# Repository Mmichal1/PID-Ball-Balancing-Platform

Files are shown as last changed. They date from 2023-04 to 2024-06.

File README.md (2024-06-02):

# PID Ball Balancing Platform

Dual-axis ball balancing platform. The ball's location on the platform, relative to the center, is detected using a vision system, while the platform's tilt is controlled by a PID controller in each axis. This controller determines the positions of the servo mechanisms to maintain the ball at the center of the platform. Image processing and the PID controllers are implemented on a Raspberry Pi 4 mini-computer with a Raspberry Pi camera, and the servo mechanisms are controlled indirectly through serial port communication with an Arduino Uno.

## Ball detection and localization

Localization of the ball is carried out by analyzing the image received from the camera using the OpenCV library. The center of the platform is determined by ArUco markers placed at the corners of the platform. The intersection of diagonals drawn from the extreme points determines the center. Then, the position of the ball in the image is determined and the vector of the ball's displacement relative to the center of the platform is established.

### Detection

The position of the ball on the image is determined in 3 steps:

- Apply mask that brings out the pixel values within the specified HSV range.

<p align="center">
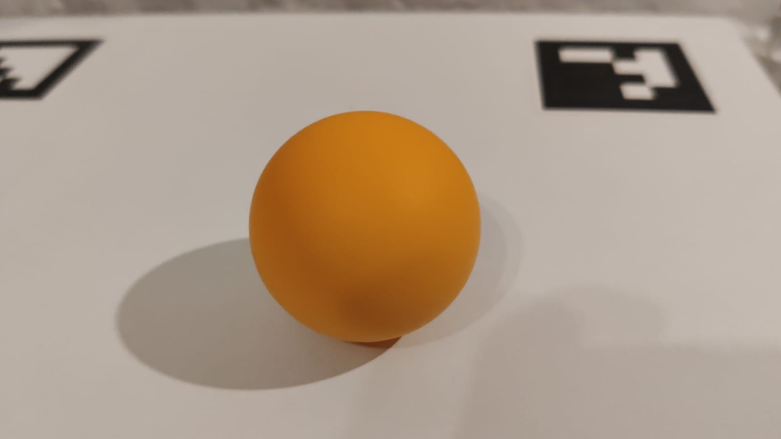
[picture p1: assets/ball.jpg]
  
</p>

<p align="center">
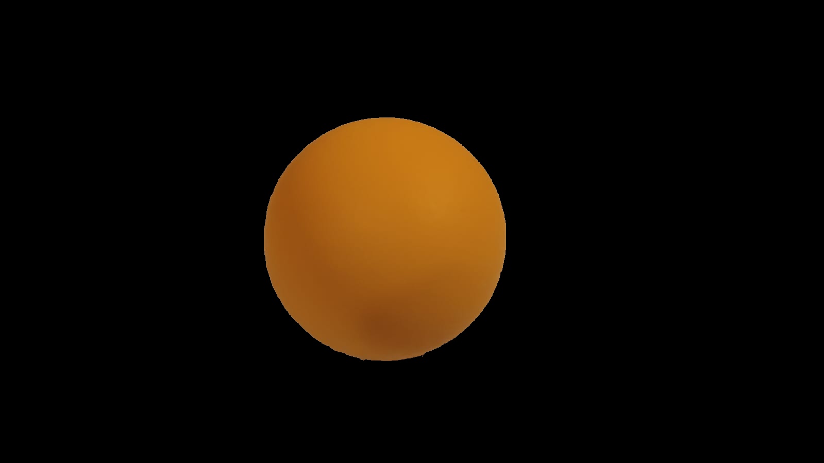
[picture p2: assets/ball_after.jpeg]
  
</p>

- Find contours on the image.
- Return the center biggest contour by area which is assumed to be the ball.

This works assuming that no objects with a color similar to the color of the ball are visible in the frame.

### Localization

The first step in the localization of the ball is determining the center of the platform. This is done using ArUco markers. After the center of the platform is determined, the distance of the ball in both axes in regard to the center of the platform is calculated.

<p align="center">
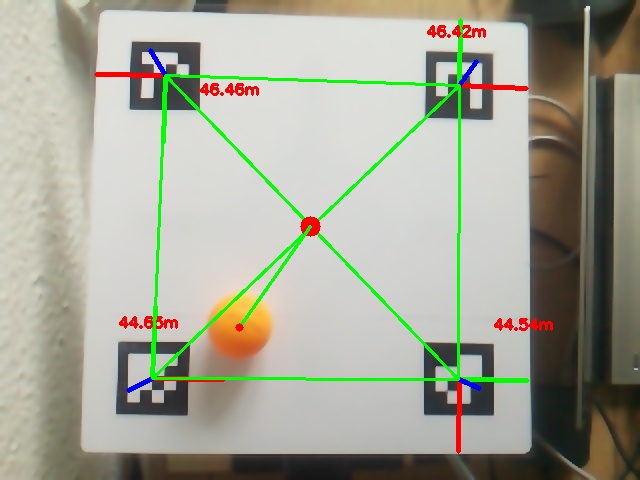
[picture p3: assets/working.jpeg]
  
</p>

The center of the platform is remembered in case any of the markers is covered by the ball.

<p align="center">
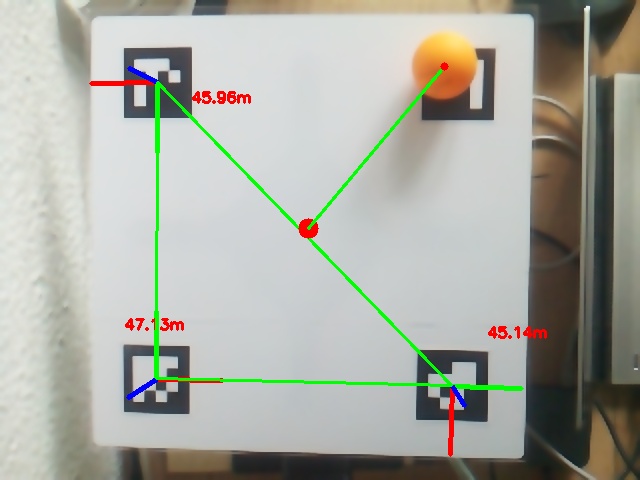
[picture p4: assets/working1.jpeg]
  
</p>

## Balancing

The ball is balanced in each axis independently by two PIDs based on the distance from the center using servomechanisms that tilt the platform accordingly. The input to the regulator is the distance from the center of the platform and the output is the position of the servomechanism. Tuning the regulator was done manually. Final regulation constants are as follows:

- Kp = 0.38
- Ki = 0.022
- Kd = 0.1

## Platform Construction

Most elements were modeled using Fusion 360 and 3D printed. All models and drawings can be found in `/technical_drawings` directory.

All elements were glued to a wooden base. The camera stand was constructed using aluminium profiles. The platform is a plexi glass panel.

<p align="center">
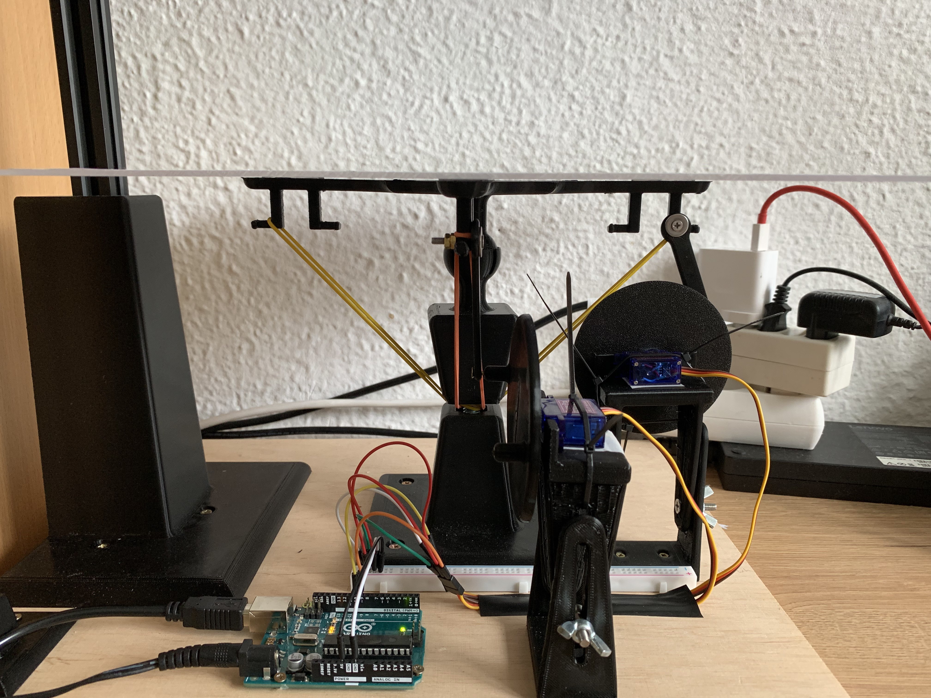
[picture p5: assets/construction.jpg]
  
</p>

<p align="center">
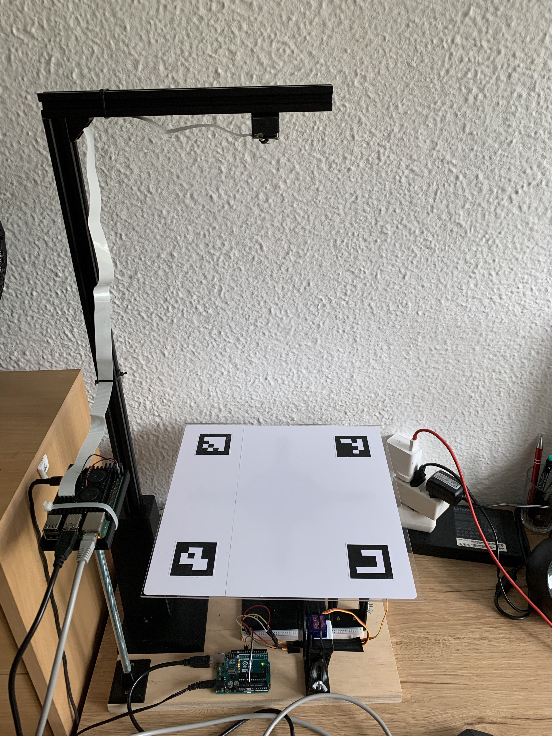
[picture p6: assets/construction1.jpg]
  
</p>

## Operation

A video showcasing the balancing platform operation has been uploaded to [YouTube](https://youtu.be/hny_5dCIR1Q).

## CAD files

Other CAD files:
technical_drawings/3d_models/Montaż_kamery.dwg
technical_drawings/3d_models/lacznik_kulkowy.dwg
technical_drawings/3d_models/Zewnetrzny_stojak.dwg
technical_drawings/3d_models/gora_platformy.dwg
technical_drawings/3d_models/Koło.dwg
technical_drawings/3d_models/wewnetrzny_stojak.dwg
technical_drawings/3d_models/Montaż_ramienia.dwg
technical_drawings/3d_models/Podstawa_platformy.dwg
technical_drawings/3d_models/Koło.ipt
technical_drawings/3d_models/Montaż_kamery.ipt
technical_drawings/3d_models/Montaż_ramienia.ipt
technical_drawings/3d_models/Podstawa_platformy.ipt
technical_drawings/3d_models/Zewnetrzny_stojak.ipt
technical_drawings/3d_models/gora_platformy.ipt
technical_drawings/3d_models/lacznik_kulkowy.ipt
technical_drawings/3d_models/podstawa raspberry.ipt
technical_drawings/3d_models/stolik raspberry.ipt
technical_drawings/3d_models/wewnetrzny_stojak.ipt

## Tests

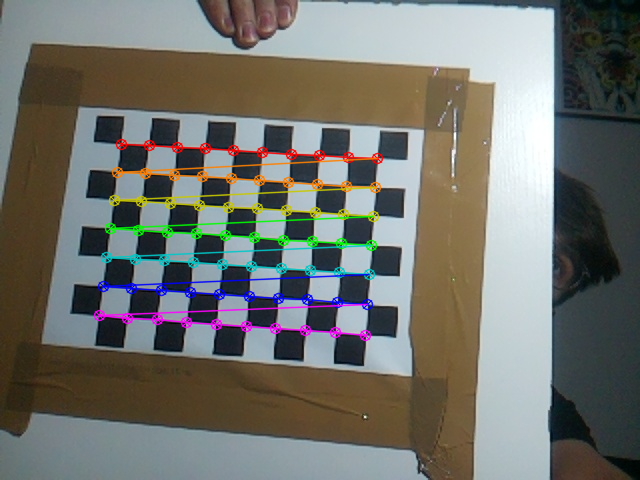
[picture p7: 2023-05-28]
camera_calibration/output_images/chessboard_corners_20230528_203139.png

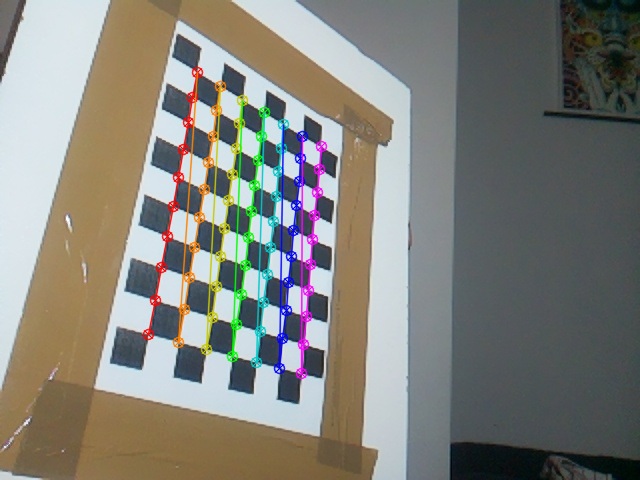
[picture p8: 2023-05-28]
camera_calibration/output_images/chessboard_corners_20230528_203134.png

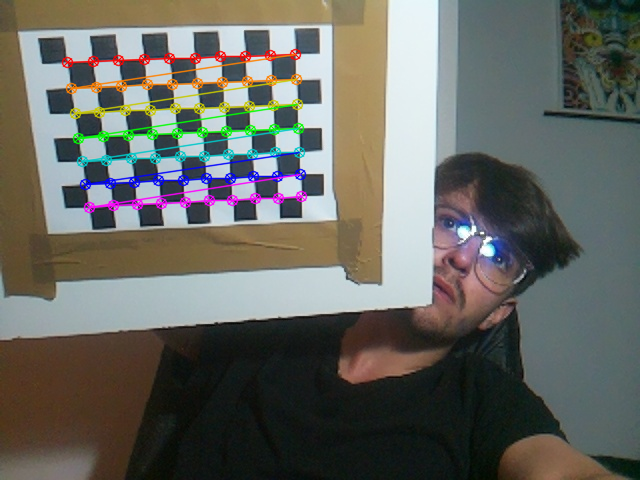
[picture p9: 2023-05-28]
camera_calibration/output_images/chessboard_corners_20230528_203137.png

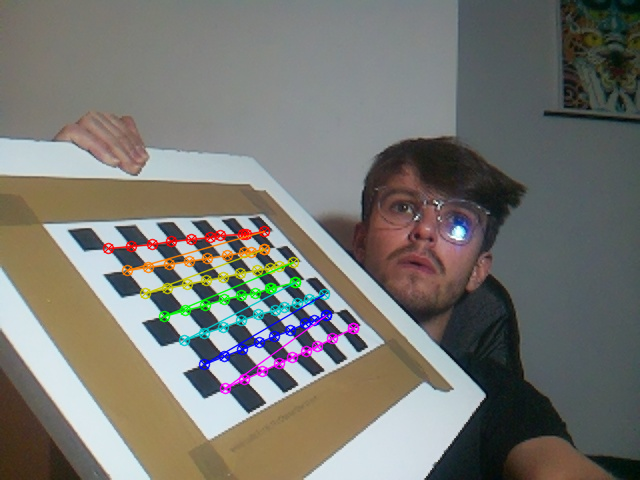
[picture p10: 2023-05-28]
camera_calibration/output_images/chessboard_corners_20230528_203148.png

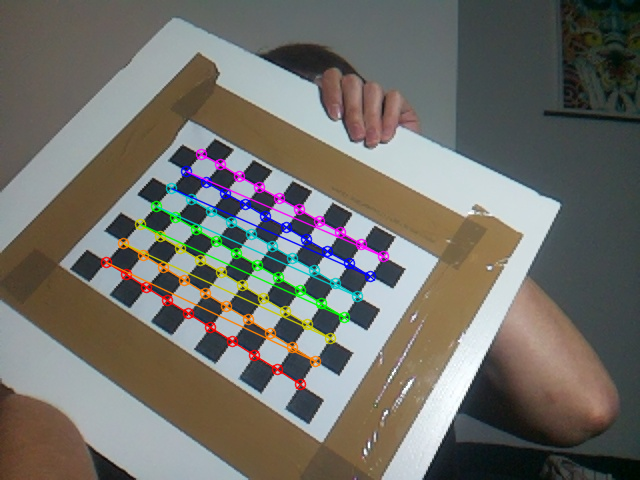
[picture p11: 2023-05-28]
camera_calibration/output_images/chessboard_corners_20230528_203145.png

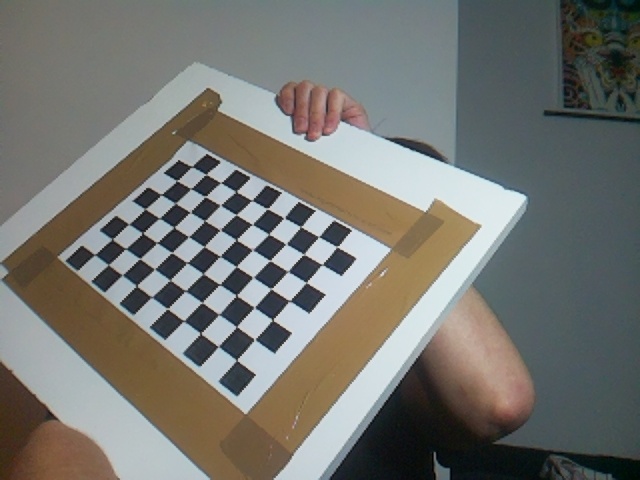
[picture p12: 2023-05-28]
camera_calibration/source_images/camera_13.jpeg

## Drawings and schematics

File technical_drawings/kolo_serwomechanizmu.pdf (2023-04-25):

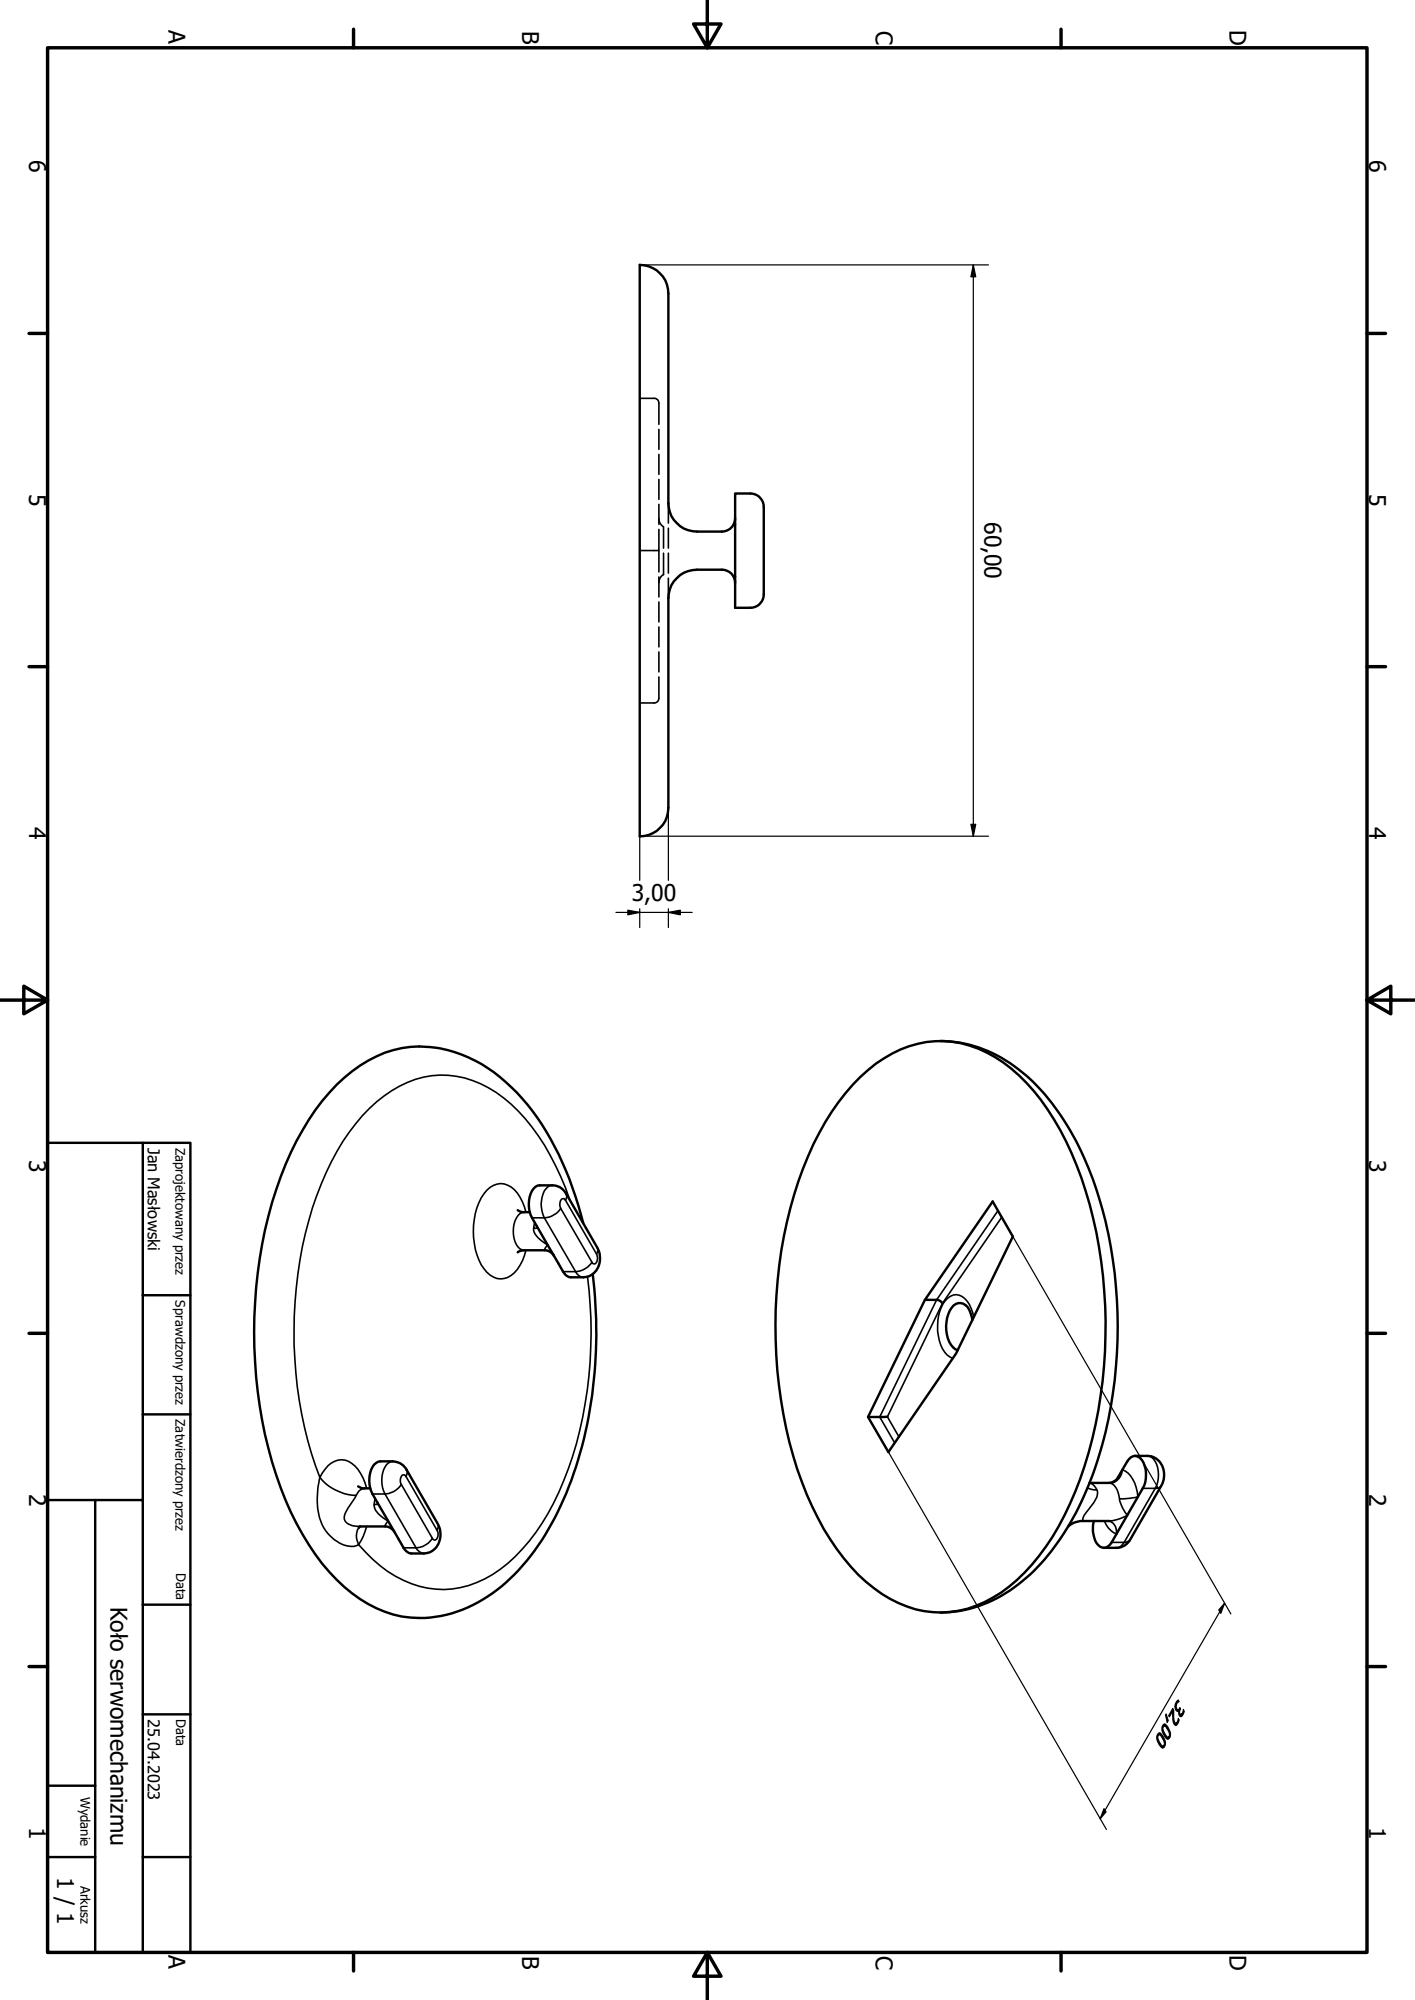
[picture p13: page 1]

11 22 33 44 55 66 A A B B C C D D Koło serwomechanizmu Jan Masłowski 25.04.2023 Zaprojektowany przez Sprawdzony przez Zatwierdzony przez Data 1 / 1 Wydanie Arkusz Data 60,00

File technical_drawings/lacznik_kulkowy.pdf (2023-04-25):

40,00 | 29,94 | 15,00

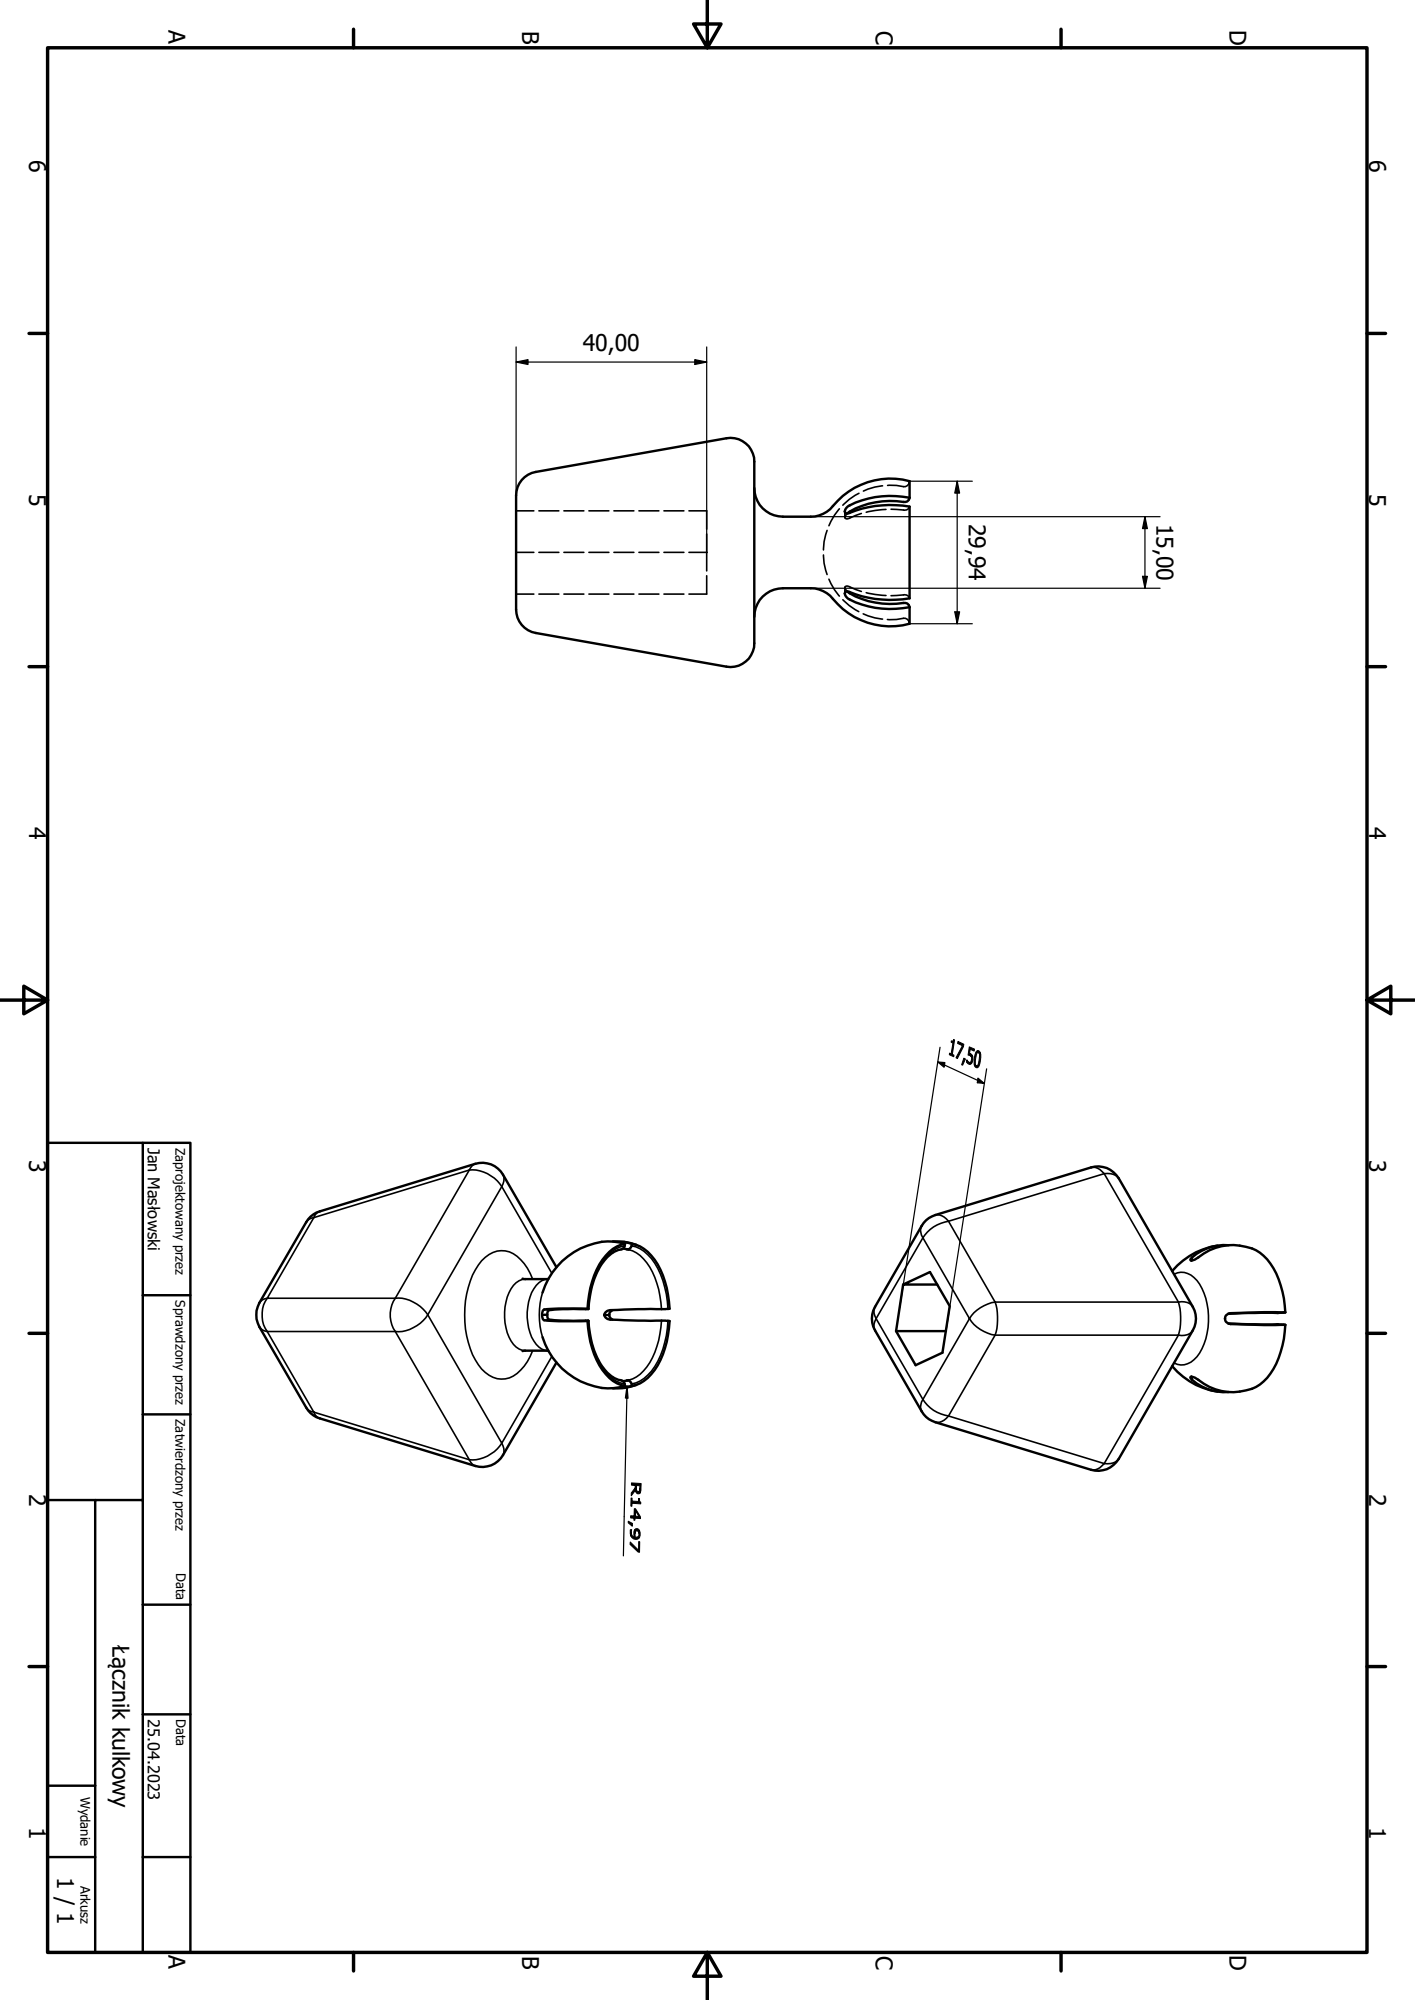
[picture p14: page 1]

D D C C B B A A 66 55 44 33 22 11 Data Arkusz Wydanie 1 / 1 Data Zatwierdzony przez Sprawdzony przez Zaprojektowany przez 25.04.2023 Jan Masłowski Łącznik kulkowy

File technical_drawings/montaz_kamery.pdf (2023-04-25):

6,00

12,17

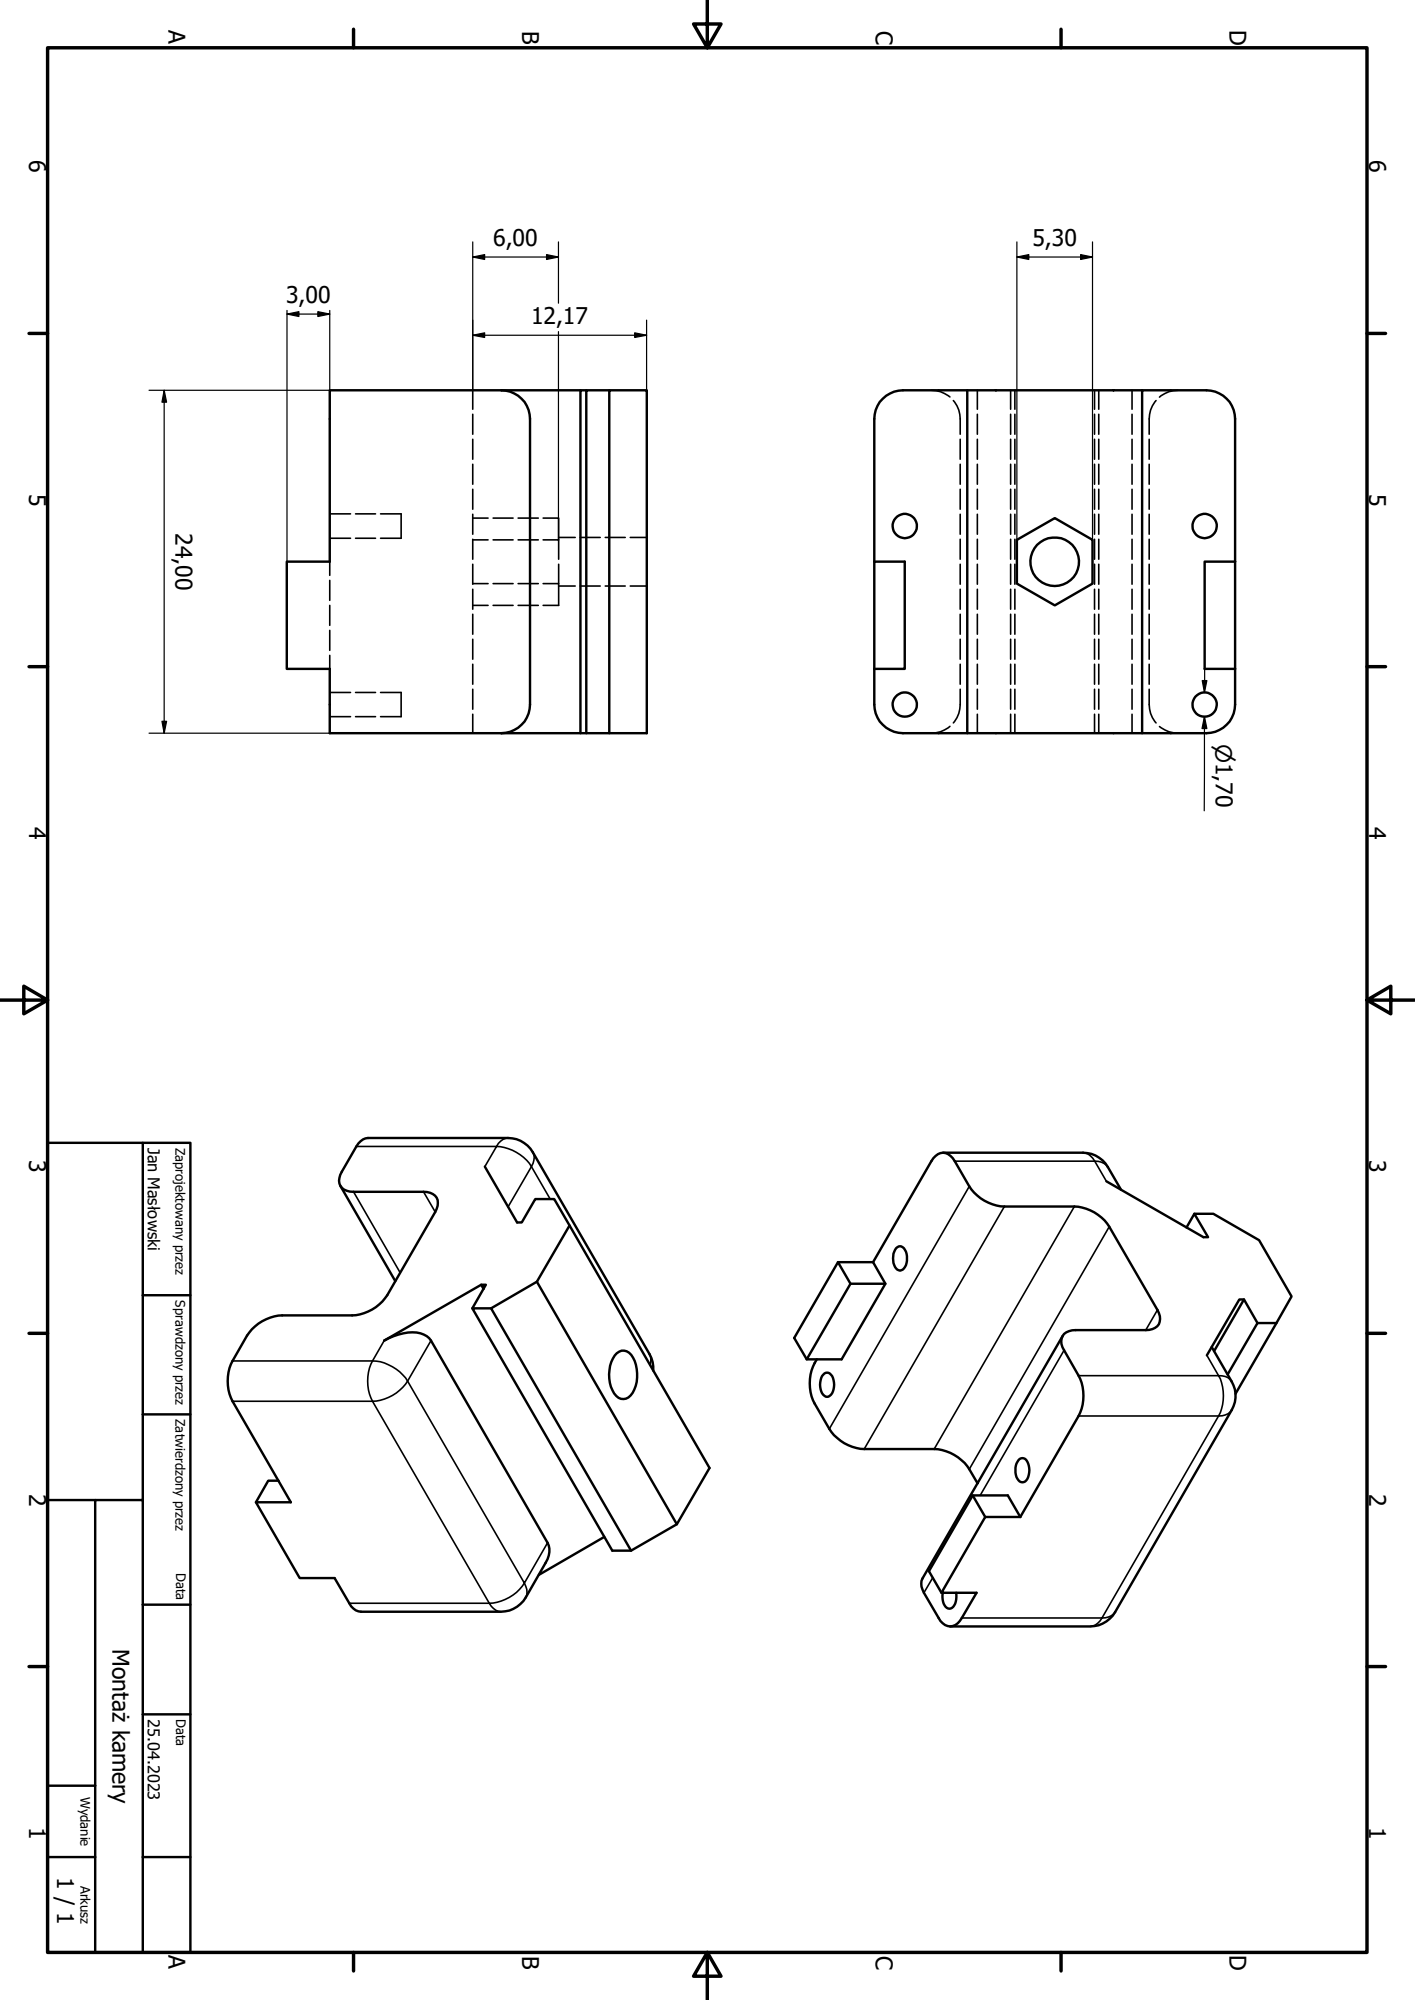
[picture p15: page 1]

11 22 33 44 55 66 A A B B C C D D Montaż kamery Jan Masłowski 25.04.2023 Zaprojektowany przez Sprawdzony przez Zatwierdzony przez Data 1 / 1 Wydanie Arkusz Data 24,00

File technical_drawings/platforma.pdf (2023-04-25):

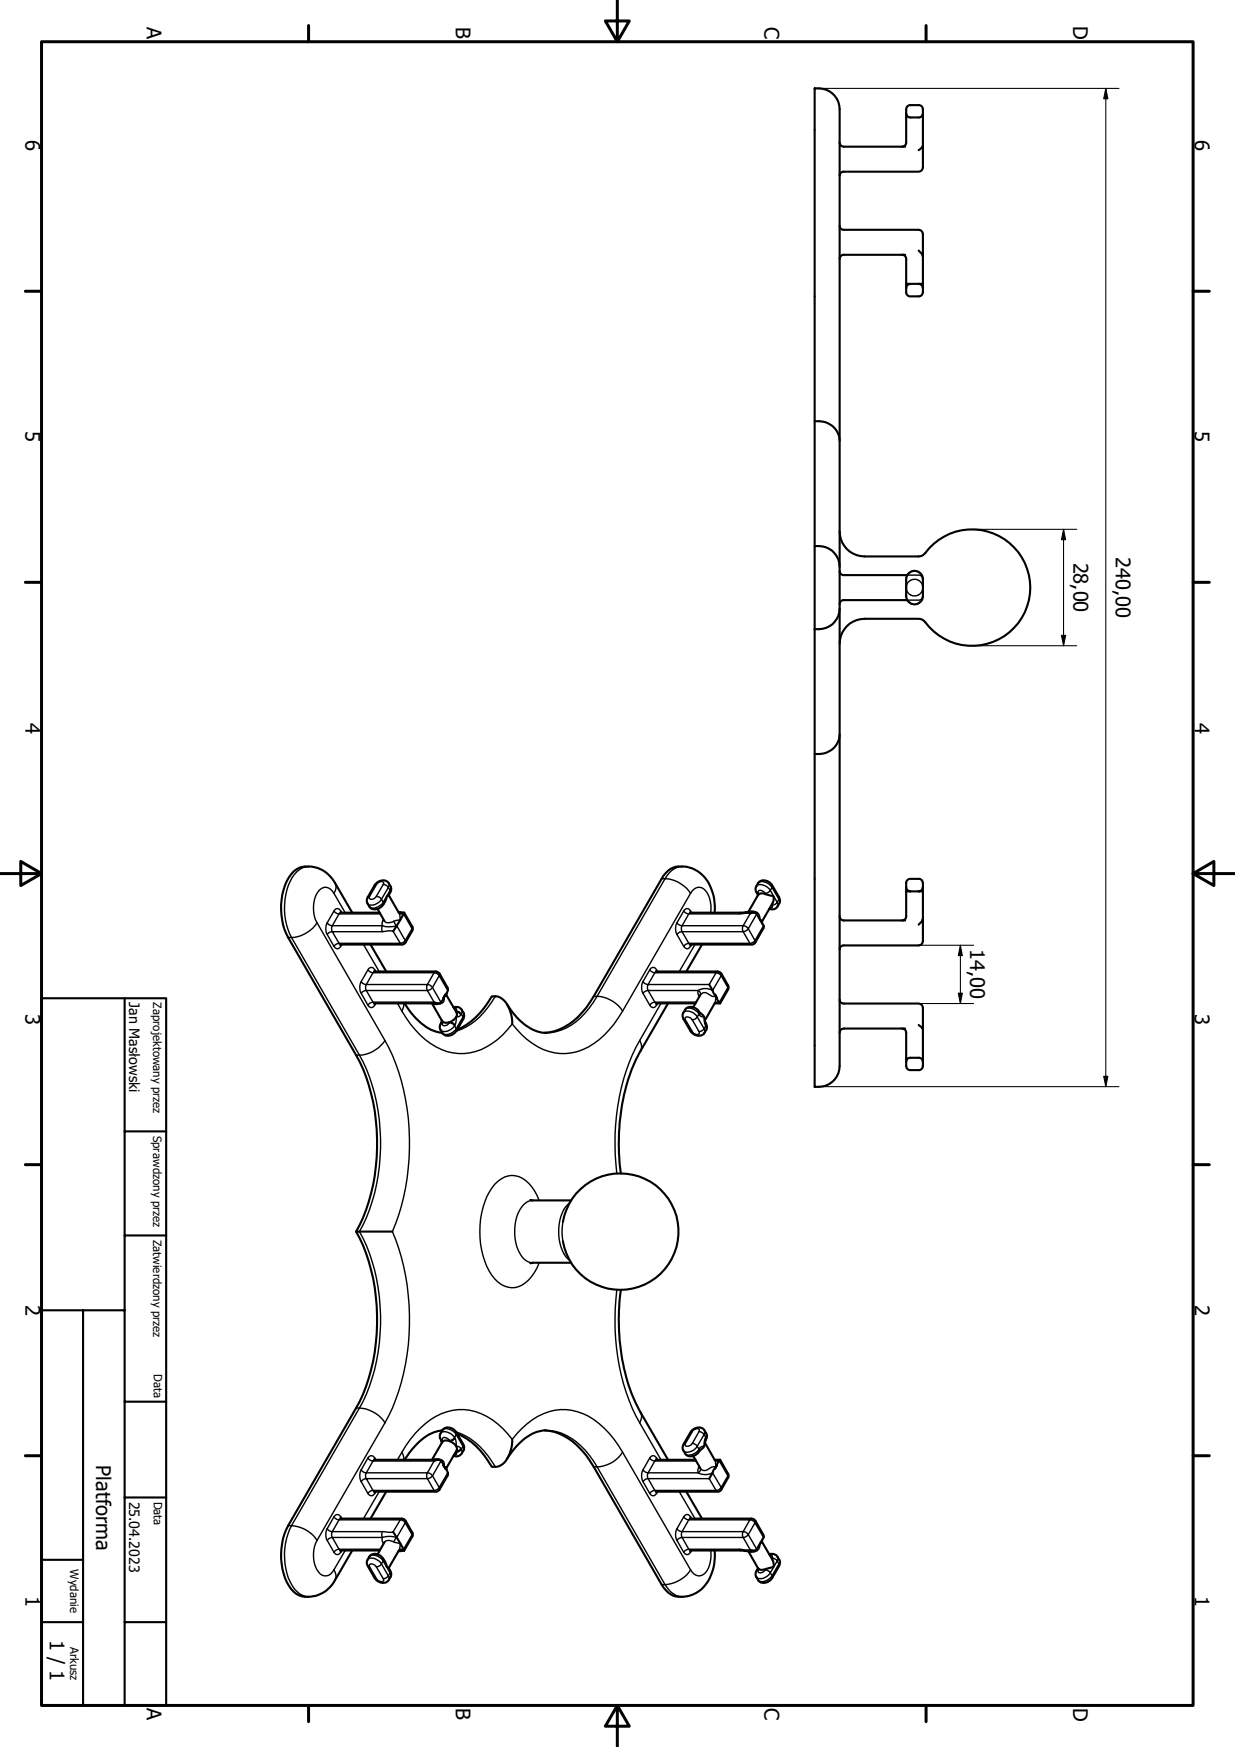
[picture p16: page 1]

11 22 33 44 55 66 A A B B C C D D Platforma Jan Masłowski 25.04.2023 Zaprojektowany przez Sprawdzony przez Zatwierdzony przez Data 1 / 1 Wydanie Arkusz Data 28,00 240,00 14,00

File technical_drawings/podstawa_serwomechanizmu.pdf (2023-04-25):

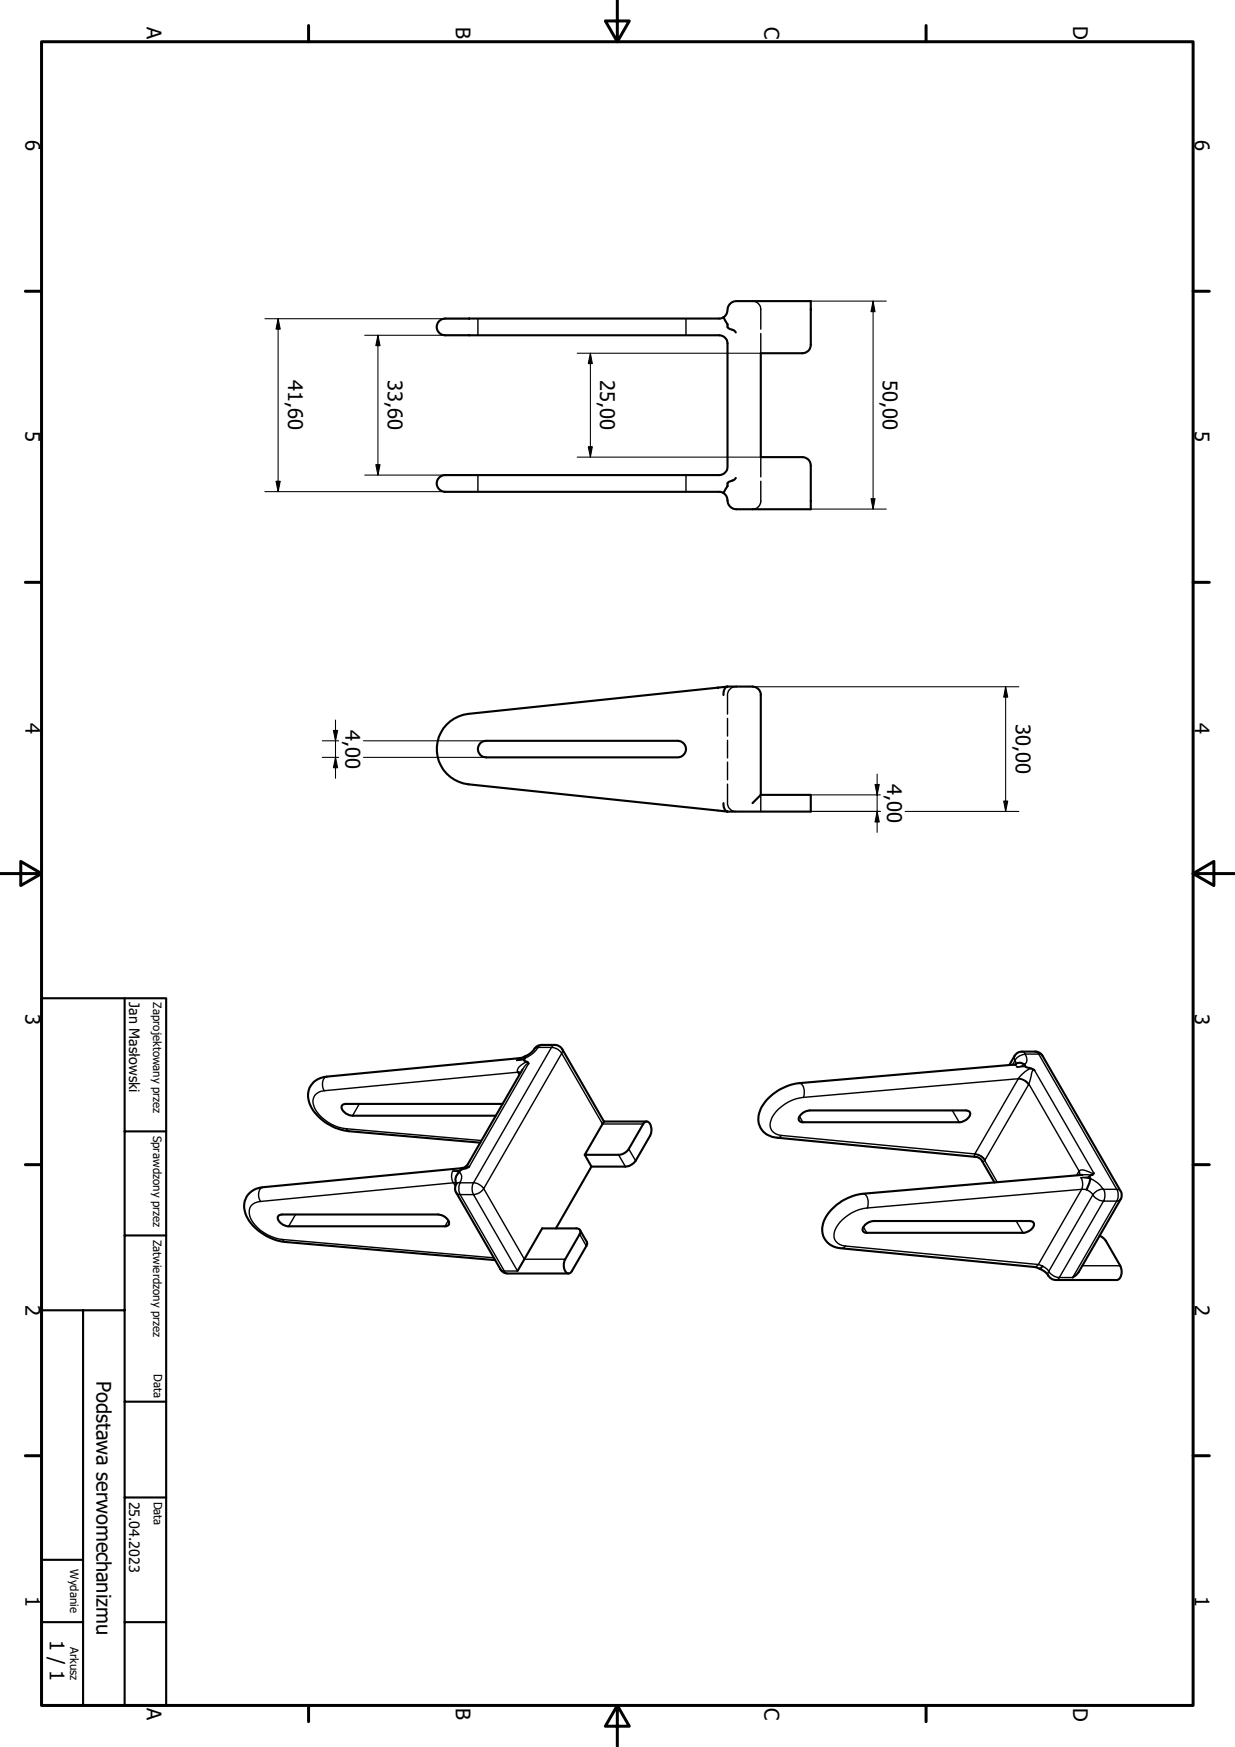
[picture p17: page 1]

11 22 33 44 55 66 A A B B C C D D Podstawa serwomechanizmu Jan Masłowski 25.04.2023 Zaprojektowany przez Sprawdzony przez Zatwierdzony przez Data 1 / 1 Wydanie Arkusz Data 41,60 33,60 25,00 4,00 4,00 50,00 30,00

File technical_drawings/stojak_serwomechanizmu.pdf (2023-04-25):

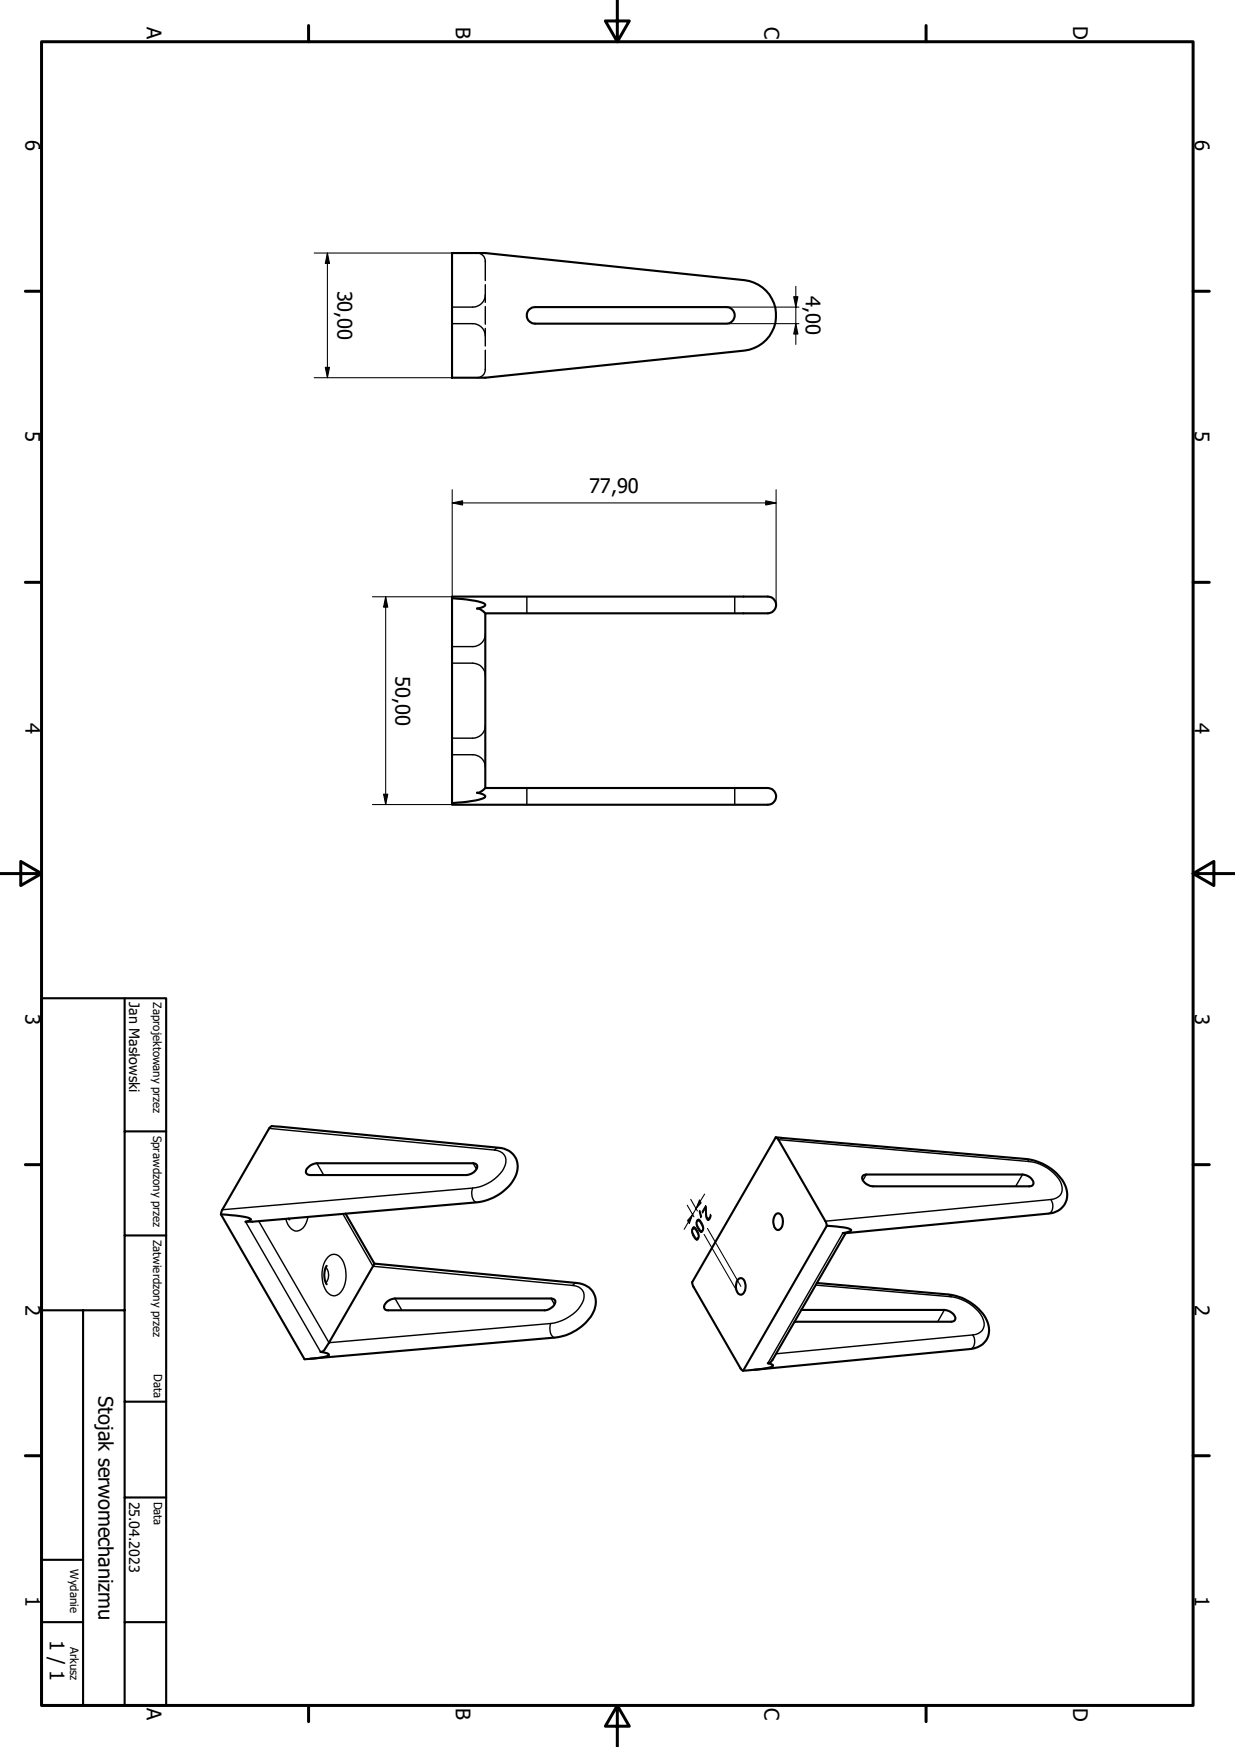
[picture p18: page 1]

11 22 33 44 55 66 A A B B C C D D Stojak serwomechanizmu Jan Masłowski 25.04.2023 Zaprojektowany przez Sprawdzony przez Zatwierdzony przez Data 1 / 1 Wydanie Arkusz Data 50,00 30,00 4,00

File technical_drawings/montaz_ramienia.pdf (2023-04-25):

60,00

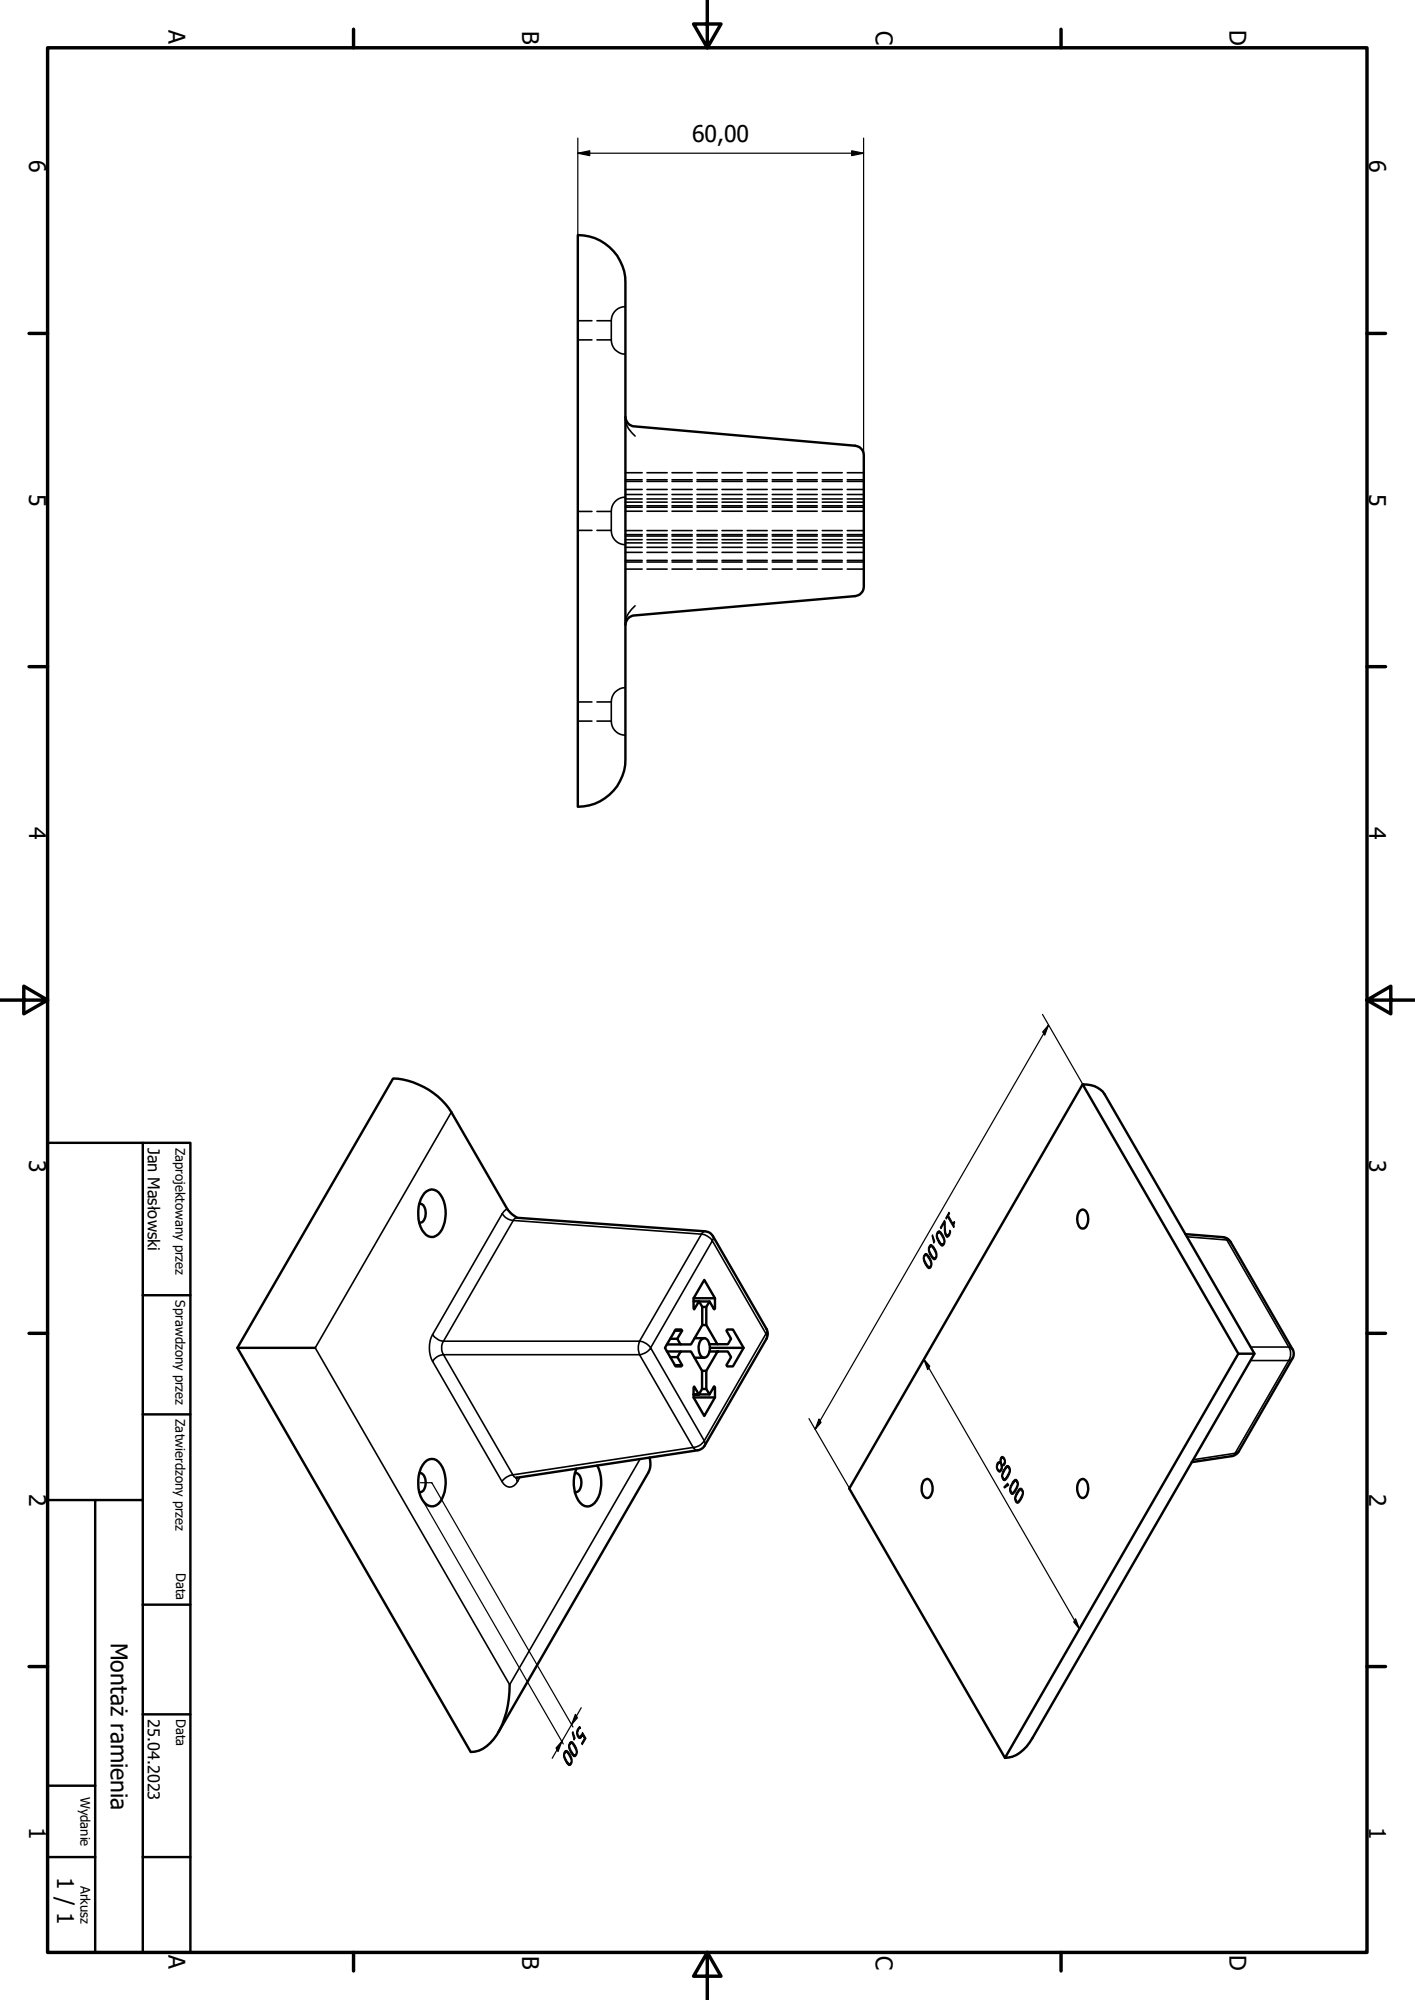
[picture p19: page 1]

11 22 33 44 55 66 A A B B C C D D Montaż ramienia Jan Masłowski 25.04.2023 Zaprojektowany przez Sprawdzony przez Zatwierdzony przez Data 1 / 1 Wydanie Arkusz Data

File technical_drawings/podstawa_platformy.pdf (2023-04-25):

70,00

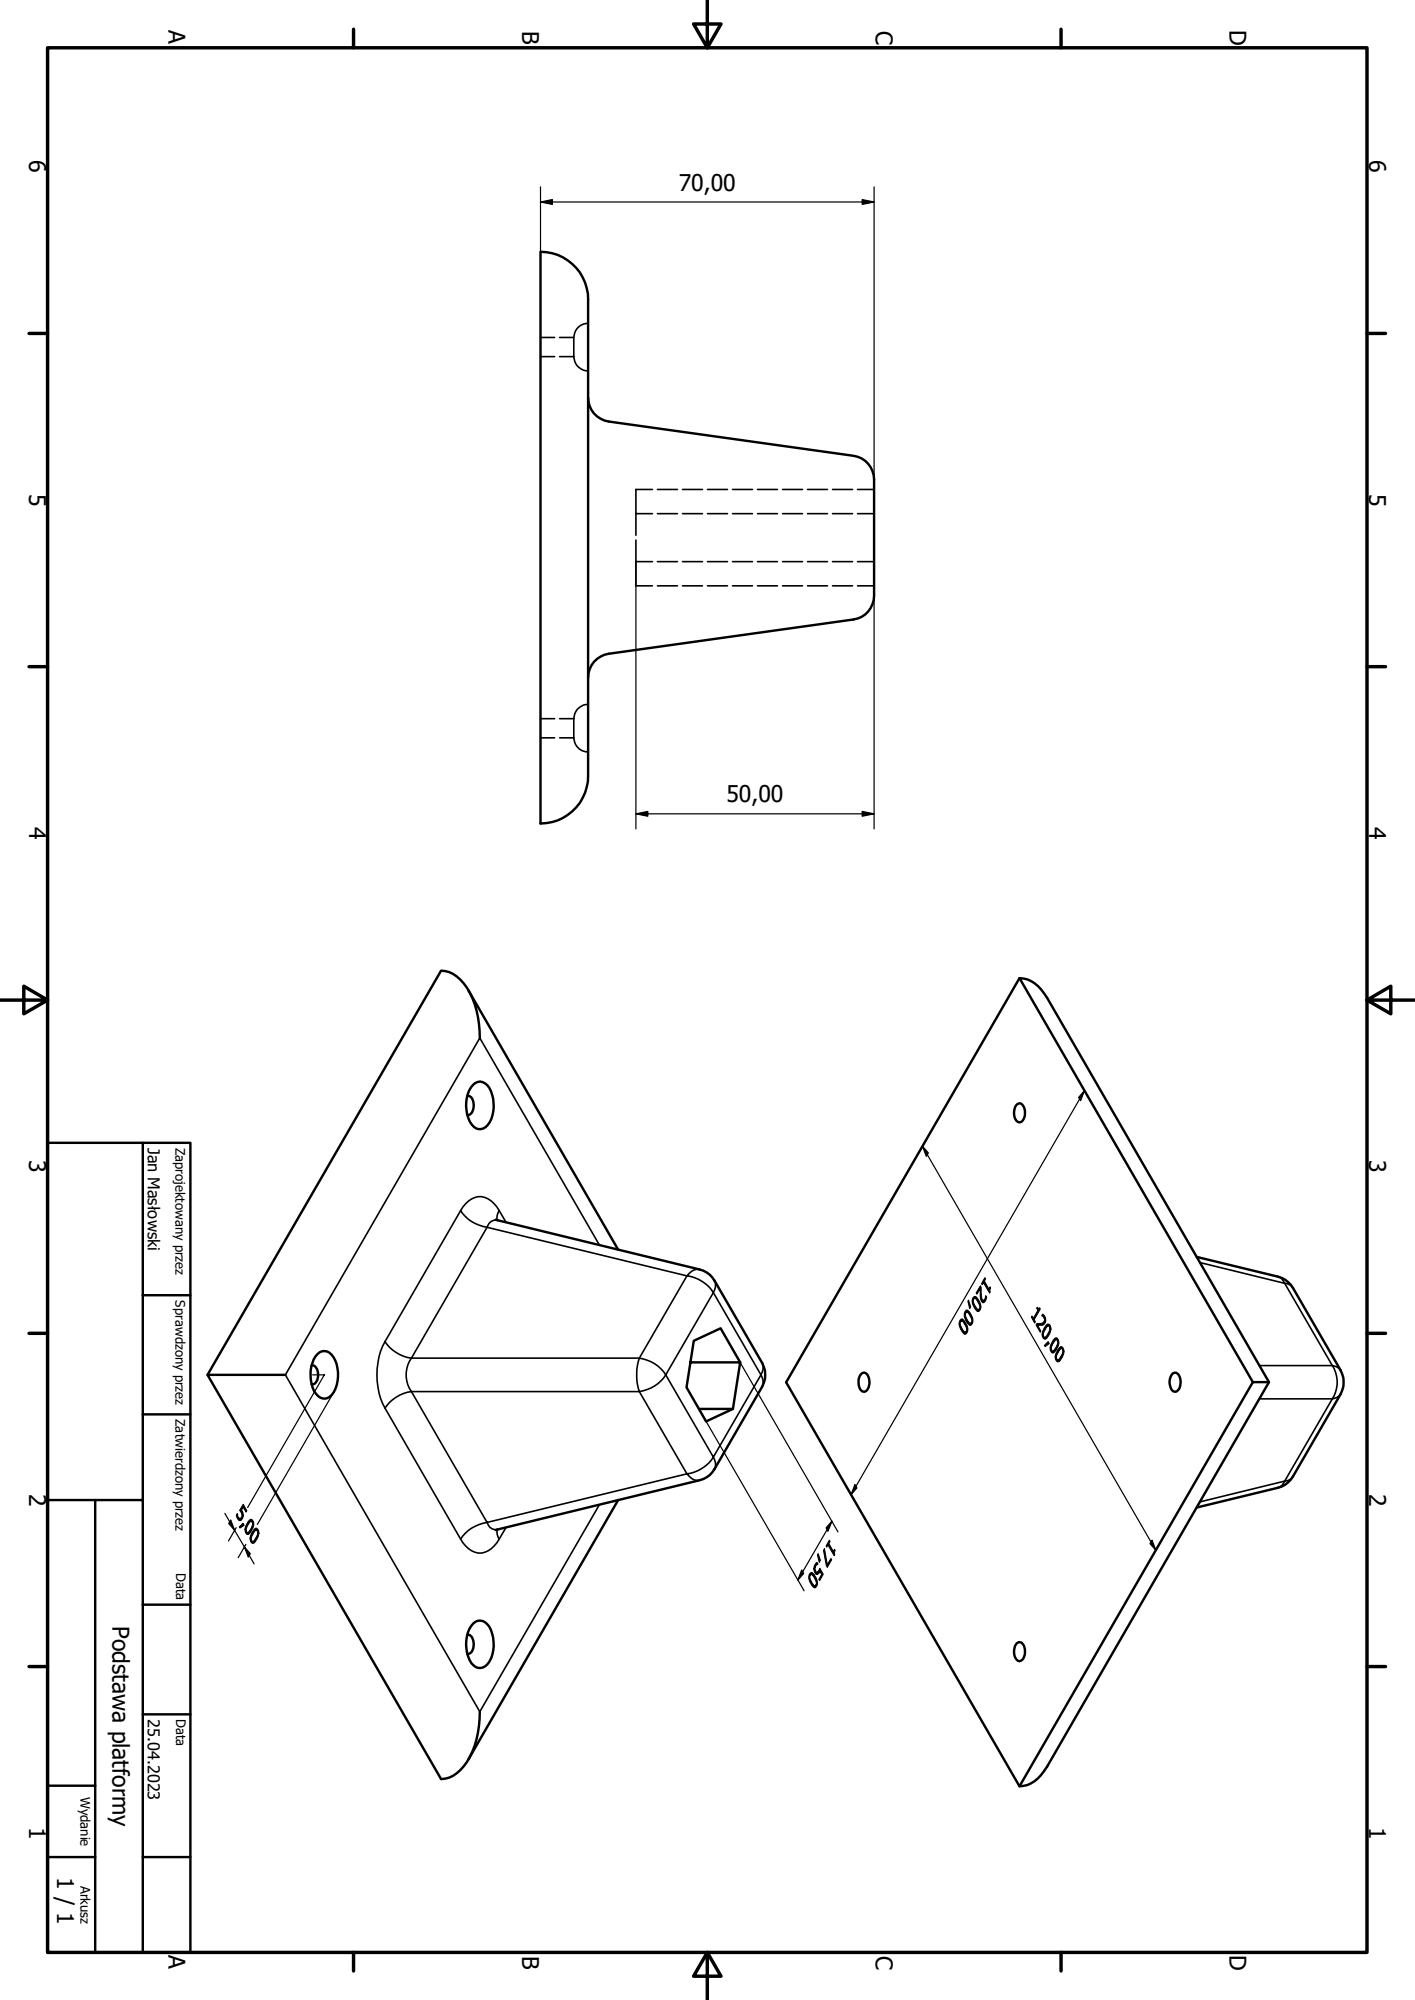
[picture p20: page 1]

11 22 33 44 55 66 A A B B C C D D Podstawa platformy Jan Masłowski 25.04.2023 Zaprojektowany przez Sprawdzony przez Zatwierdzony przez Data 1 / 1 Wydanie Arkusz Data

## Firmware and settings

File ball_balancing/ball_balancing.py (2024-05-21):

from picamera2 import Picamera2
import time
import cv2 as cv
import json
import numpy as np
import serial
from ball_balancing.pid import PID
from segment import Segment
from datetime import datetime

# Initial platform center position
platform_center = (300, 230)
previous_platform_center = (300, 230)

# Platform center boundaries
x_boundaries = (280, 330)
y_boundaries = (200, 260)

# Ball position boundaries
ball_x_boundaries = (-220, 220)
ball_y_boundaries = (-220, 220)

# Loop refresh rate
period = 0.05


def get_ball_dist_from_center(frame, matrix_coeff, distortion_coeff, aruco_detector):
    # Constants
    known_ball_size = 3.8
    marker_size_cm = 4.7

    list_of_segments = []

    # This filter blurs all the details but leaves the contours
    # so that processing the frame to find markers is easier and
    # more accurate
    frame = cv.bilateralFilter(frame, 9, 100, 100)

    # Process the frame, get the ball position and mark it on the frame
    ball_coordinates = detect_ball(frame)

    # Make the frame grayscale as the program doesn't need RGB values
    gray = cv.cvtColor(frame, cv.COLOR_BGR2GRAY)

    # Detect markers in the freme
    marker_corners, marker_ids, _ = aruco_detector.detectMarkers(gray)

    if len(marker_corners) > 0:
        global platform_center
        global previous_platform_center
        markers_center = []
        marker_ids = marker_ids.flatten()

        # Estimate pose of the markers in relation to the camera position
        rvec, tvec, _ = cv.aruco.estimatePoseSingleMarkers(
            marker_corners, marker_size_cm, matrix_coeff, distortion_coeff
        )

        for marker_corner, _, i in zip(marker_corners, marker_ids, range(0, marker_ids.size)):
            # Draw frame axes for each marker
            cv.drawFrameAxes(frame, matrix_coeff, distortion_coeff, rvec[i], tvec[i], marker_size_cm)

            # Find and save markers center
            (top_left, top_right, bottom_right, bottom_left) = marker_corner.reshape((4, 2))
            top_right = (int(top_right[0]), int(top_right[1]))
            bottom_right = (int(bottom_right[0]), int(bottom_right[1]))
            bottom_left = (int(bottom_left[0]), int(bottom_left[1]))
            top_left = (int(top_left[0]), int(top_left[1]))
            cX = int((top_left[0] + bottom_right[0]) / 2.0)
            cY = int((top_left[1] + bottom_right[1]) / 2.0)
            markers_center.append((cX, cY))

            # Get marker distance from the camera and write in on the frame
            distance = np.sqrt(tvec[i][0][2] ** 2 + tvec[i][0][0] ** 2 + tvec[i][0][1] ** 2)
            cv.putText(
                frame, f"{distance:.2f}m", (top_left[0], top_left[1] - 15), cv.FONT_HERSHEY_SIMPLEX, 0.5, (0, 0, 255), 2
            )

        # Find all segments from every marker to every other one and save each segment data
        if len(marker_corners) > 1:
            for i in range(len(marker_ids)):
                for j in range(i + 1, len(marker_ids)):
                    # Calculate the segments length
                    distance = np.linalg.norm(tvec[i] - tvec[j])
                    cv.line(frame, markers_center[i], markers_center[j], (0, 255, 0), 2)
                    list_of_segments.append(
                        Segment(
                            length=distance,
                            start_point=(markers_center[i]),
                            end_point=(markers_center[j]),
                            start_tvec=(tvec[i]),
                            end_tvec=(tvec[j]),
                        )
                    )

            if len(list_of_segments) > 1:
                # Sort the segments by their length
                sorted_segments = sorted(list_of_segments, key=lambda p: p.length, reverse=True)
                # The platform center will be the intersection between two longest segments which will be the diagonals
                platform_center = find_intersection(sorted_segments[0], sorted_segments[1])

                # Check if the platform center is within the possible coordinates if not then keep the previous calculated center as the current one
                if not (
                    platform_center[0] > x_boundaries[0]
                    and platform_center[0] < x_boundaries[1]
                    and platform_center[1] > y_boundaries[0]
                    and platform_center[1] < y_boundaries[1]
                ):
                    platform_center = previous_platform_center

                previous_platform_center = platform_center
            else:
                platform_center = previous_platform_center

        else:
            platform_center = previous_platform_center

        # Mark platform center on the frame
        cv.circle(frame, platform_center, 10, (0, 0, 255), -1)

        # If the ball is within the frame and platform boundaries then calculate the ball coordinates
        if ball_coordinates is not None:
            cv.line(frame, platform_center, ball_coordinates, (0, 255, 0), 2)
            result = tuple(x - y for x, y in zip(platform_center, ball_coordinates))
            cv.circle(frame, ball_coordinates, 4, (0, 0, 255), -1)

            if (
                result[0] > ball_x_boundaries[0]
                and result[0] < ball_x_boundaries[1]
                and result[1] > ball_y_boundaries[0]
                and result[1] < ball_y_boundaries[1]
            ):
                return frame, result

    return frame, (0, 0)


def detect_ball(frame):
    # Convert the image to HSV color space
    hsv = cv.cvtColor(frame, cv.COLOR_BGR2HSV)

    # Define the lower and upper bounds for the ball color
    lower_color = np.array([0, 150, 120])
    upper_color = np.array([180, 255, 255])

    # Create a mask for the ball color
    mask = cv.inRange(hsv, lower_color, upper_color)

    # Apply morphological operations to remove noise
    kernel = cv.getStructuringElement(cv.MORPH_ELLIPSE, (5, 5))
    mask = cv.morphologyEx(mask, cv.MORPH_OPEN, kernel)
    mask = cv.morphologyEx(mask, cv.MORPH_CLOSE, kernel)

    # Find contours of the ball
    contours, _ = cv.findContours(mask, cv.RETR_EXTERNAL, cv.CHAIN_APPROX_SIMPLE)

    # Find the largest contour (assumed to be the ball)
    if len(contours) > 0:
        ball_contour = max(contours, key=cv.contourArea)
        (x, y), _ = cv.minEnclosingCircle(ball_contour)
        return (int(x), int(y))

    return None


def find_intersection(segment_one, segment_two):
    # Read points coordinates
    x1, y1 = segment_one.start_point
    x2, y2 = segment_one.end_point
    x3, y3 = segment_two.start_point
    x4, y4 = segment_two.end_point

    # Calculate the intersection point
    px = ((x1 * y2 - y1 * x2) * (x3 - x4) - (x1 - x2) * (x3 * y4 - y3 * x4)) / (
        (x1 - x2) * (y3 - y4) - (y1 - y2) * (x3 - x4)
    )
    py = ((x1 * y2 - y1 * x2) * (y3 - y4) - (y1 - y2) * (x3 * y4 - y3 * x4)) / (
        (x1 - x2) * (y3 - y4) - (y1 - y2) * (x3 - x4)
    )

    return (int(px), int(py))


def main(args=None):
    # PID constants
    k_p = 0.38
    k_i = 0.022
    k_d = 0.1
    setpoint = 0

    # Init serial port connection
    serial_port = serial.Serial("/dev/ttyACM0", 9600, timeout=1)
    serial_port.reset_input_buffer()
    # Send signal to level the platform
    serial_port.write(b"60,65\n")

    # Create PID instances for each axis
    PID_x = PID(
        k_p=k_p,
        k_i=k_i,
        k_d=k_d,
        setpoint=setpoint,
        servo_lower_bound=51,
        servo_upper_bound=80,
        period=period,
        integral_bounds=40,
    )
    PID_y = PID(
        k_p=k_p,
        k_i=k_i,
        k_d=k_d,
        setpoint=setpoint,
        servo_lower_bound=41,
        servo_upper_bound=78,
        period=period,
        integral_bounds=40,
    )

    # Init aruco detector
    arucoDictionary = cv.aruco.getPredefinedDictionary(cv.aruco.DICT_4X4_250)
    arucoParameters = cv.aruco.DetectorParameters()
    arucoDetector = cv.aruco.ArucoDetector(arucoDictionary, arucoParameters)

    # Init and configure PiCamera
    camera = Picamera2()
    camera.preview_configuration.main.size = (640, 480)
    camera.preview_configuration.main.format = "RGB888"
    camera.preview_configuration.align()
    camera.configure("preview")
    camera.start()

    # Read camera parameters received from camera calibration
    with open("../camera_calibration/camera.json", "r") as json_file:
        camera_data = json.load(json_file)
        dist = np.array(camera_data["dist"])
        mtx = np.array(camera_data["mtx"])

    # Wait for camera to be ready
    time.sleep(0.01)

    # Main program loop
    while True:
        # Capture frame, process it to find markers then the platform center and ball coordinates in
        # relation to the platform center. Mark all markers, ball position, platform center and all lines
        # on the frame
        frame, result = get_ball_dist_from_center(camera.capture_array(), mtx, dist, arucoDetector)

        print(f"Ball coordinates: {result}")

        # Get values that should be sent to the servos based on the distance in each axis from the center
        servo_value_y = PID_y.regulate(-result[0])
        servo_value_x = PID_x.regulate(result[1])
        serial_port.write(b"%d,%d\n" % (servo_value_y, servo_value_x))

        # Show camera feed in a separate window
        cv.imshow("Camera", frame)
        key = cv.waitKey(1) & 0xFF
        if key == ord("q"):
            break
        if key == ord("c"):
            cv.imwrite(f"output_images/camera_{datetime.now().strftime('%H%M%S')}.jpeg", frame)

        # Wait to enter the next iteration
        time.sleep(period)

    cv.destroyAllWindows()


if __name__ == "__main__":
    main()

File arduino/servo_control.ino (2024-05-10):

#include <Servo.h>

Servo myservo_1;
Servo myservo_2;

int servo_1_angle = 60;
int servo_2_angle = 65;

void setup() {
    myservo_1.attach(9);
    myservo_2.attach(10);
    Serial.begin(9600);  
}

void loop() {
    if (Serial.available()) {
        String data = Serial.readStringUntil('\n'); 

        int separatorIndex = data.indexOf(',');
        if (separatorIndex != -1) {
            String Str1 = data.substring(0, separatorIndex);
            String Str2 = data.substring(separatorIndex + 1); 
            Serial.println(data);
            servo_1_angle = Str1.toInt();
            servo_2_angle = Str2.toInt();
        }

        myservo_1.write(servo_1_angle);
        myservo_2.write(servo_2_angle);
    }
}

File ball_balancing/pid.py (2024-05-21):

class PID:
    def __init__(
        self,
        k_p: float,
        k_i: float,
        k_d: float,
        setpoint: int,
        period: float,
        servo_upper_bound: int,
        servo_lower_bound: int,
        integral_bounds: int,
    ):
        self.k_p = k_p
        self.k_i = k_i
        self.k_d = k_d
        self.setpoint = setpoint
        self.period = period
        self.integral_bounds = integral_bounds
        self.servo_lower_bound = servo_lower_bound
        self.servo_upper_bound = servo_upper_bound
        self.PID_p = 0.0
        self.PID_i = 0.0
        self.PID_d = 0.0
        self.PID_total = 0.0
        self.distance_previous_error = 0.0
        self.distance_error = 0.0

    def _map_value(self, value, in_min, in_max, out_min, out_max):
        return (value - in_min) * (out_max - out_min) / (in_max - in_min) + out_min

    def regulate(self, setpoint_error: int):
        self.distance_error = self.setpoint - setpoint_error
        # Proportional
        self.PID_p = self.k_p * self.distance_error

        # Integral
        if -self.integral_bounds < self.distance_error < self.integral_bounds:
            self.PID_i += self.k_i * self.distance_error
        else:
            self.PID_i = 0

        # Derivative
        self.PID_d = self.k_d * ((self.distance_error - self.distance_previous_error) / self.period)

        self.PID_total = self.PID_p + self.PID_i + self.PID_d
        self.PID_total = self._map_value(self.PID_total, -190, 190, self.servo_lower_bound, self.servo_upper_bound)

        if self.PID_total < self.servo_lower_bound:
            self.PID_total = self.servo_lower_bound
        if self.PID_total > self.servo_upper_bound:
            self.PID_total = self.servo_upper_bound

        print(f"Y PID_p: {self.PID_p},\nY PID_i: {self.PID_i},\nY PID_d: {self.PID_d},\nY TOTAL:{int(self.PID_total)}")

        self.distance_previous_error = self.distance_error

        return int(self.PID_total)

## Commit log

2023-04-25 add correct directory | add gitignore
    [Montaż_ramienia.dwg, Montaż_ramienia.ipt, Podstawa_platformy.dwg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]
2023-04-25 Rysunki i projekty elementów konstrukcji część 2
    [gora_platformy.dwg, gora_platformy.ipt, lacznik_kulkowy.dwg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]
2023-04-25 Rysunki techniczne i projekty konstrukcji część 3
    [Koło.dwg, Koło.ipt, Montaż_kamery.dwg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]
2023-04-25 Rysunki i projekty elementów konstrukcji część 4
    [Zewnetrzny_stojak.dwg, Zewnetrzny_stojak.ipt, wewnetrzny_stojak.dwg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]
2023-04-25 add camera calibration scripts | calibrate camera
2023-04-25 add pose estimation | add sample images
2023-05-19 change names
    [Koło.dwg, Koło.ipt, Montaż_kamery.dwg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]
2023-05-28 redo calibration | small changes
2023-06-04 testing servo control
2023-06-04 pid v1
2023-06-04 pid for one axle | need to fine tune constants
2023-06-04 add pid for the x axle
2023-06-04 initial tune for the x axis
2023-06-05 clean-up and minor fixes
    [ball_balancing.py, detectAruco.py, servo_control.ino]
2024-05-10 update gitignore | rename and move files
    [Koło.dwg, Koło.ipt, Montaż_kamery.dwg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]
